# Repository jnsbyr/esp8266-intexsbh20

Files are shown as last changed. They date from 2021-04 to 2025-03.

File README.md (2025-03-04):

# MQTT WiFi remote control for Intex PureSpa whirlpools



### Table of contents

[1. Compatibility](#compatibility)  
[2. Introduction](#introduction)  
[3. Motivation](#motivation)  
[4. Hacking the SB-H20](#hacking-the-sb-h20)  
[5. Building your own WiFi remote control](#building-your-own-wifi-remote-control)  
[6. Contributing](#contributing)  
[7. Licenses and Credits](#licenses-and-credits)

## Compatibility

This projects was originally designed for the Intex PureSpa SB-H20 but it also
supports other models:

 Model                    | Define [^1]  | Notes
 ------------------------ |:------------ |:---------------------------------------------------
 Intex PureSpa SB-H20     | MODEL_SB_H20 | supported
 Intex SimpleSpa SB–B20   | MODEL_SB_H20 | reported to be compatible, see [issue #5](../../issues/5)
 Intex PureSpa SSP-H-20-1 | MODEL_SB_H20 | supported, see [issue #53](../../issues/53)
 Intex PureSpa SJB-HS     | MODEL_SJB_HS | supported, see [issue #13](../../issues/13)

[^1]: #define required for build (see [common.h](src/esp8266-intexsbh20/common.h))

## Introduction

The Intex PureSpa models listed under [Compatibility](#compatibility) are
standalone systems that do not have a remote control option. This projects
provides information about the required hardware and software to provide
WiFi remote control using the [MQTT](https://mqtt.org/) protocol.

This is no ready-to-use product. The acquisition of the required hardware
components, their assembly and programming requires some experience with DIY
 electronics. Helpful details can also be found in the
[issues](../../issues) of this project
(e.g. a table of the hardware components not shown in the schematic can be
found in [issue #2](../../issues/2)).

> :warning: **WARNING**: If you decide to implement the presented solution
  you will void the warranty of your pool as it requires invasive
  modifications. You may only **USE THIS PROJECT AT YOUR OWN RISK**. The
  information provided is meant to be helpful but may contain errors or may be
  misinterpreted. Neither myself nor any of the contributors to this project
  provide any warranty or will assume any responsibility for any damage you
  cause yourself or others by using this project.

## Motivation

Reading the user manual of the Intex PureSpa SB-H20 was a mistake. Everyone
who has ever read a user manual knows this. They just contain things you don't
want to know.

This model seems to be designed for daily attention. It is no news that the
water of a pool should be run through a filter at least once or twice a day.
Many pools have a timer for this, but not this one.

You could keep the circulation on permanently, but this wastes more than 1 kWh
per day with the filter pump consuming around 60 W.

Somehow it should be possible to add a circulation pump timer. And if this can
be done then the water temperature could also be controlled, thus combining power
saving and comfort. Depending on the temperature profile you choose the energy
saving can be really significant compared to a constant temperature setting
because the heater consumes around 2 kW.

## Hacking the SB-H20

Opening the lid of the control panel and attaching a WiFi MCU in parallel to the
buttons was the first idea that came mind. This was possible with the predecessors
of this model, but not so with the control panel of the SB-H20. After testing around
the edges of the case with my pry tools it became obvious that the lid is probably
glued shut. If you want to open it anyway you might consider drilling holes into
the sides of the case first to get better leverage for prying but I did not want
to go that way.

Opening the pump unit and modifying the mainboard did not seem to be a good
alternative either. But there is a cable between the pump unit and the control
panel that might be tapped. Looking around I found the project
[diyscip](https://github.com/YorffoeG/diyscip) from Geoffroy Hubert that gave me
hope. Geoffroy did a splendid job with his reverse engineering but his project
is about the SSP and SJB whirlpool models.

Using a multimeter, a scope and a logic analyser helped to establish several
facts:

- there seems to be a good enough isolation between the mains and the signal lines
  (no guarantee whatsoever)
- the plug and the pinout of the SB-H20 control panel are identical to the SSP
  and SJB models
- most of the decoding of the signals from the mainboard to the control panel
  is identical or at least similar to the SSP and SJB models
- the original control panel and an additional remote control unit can be attached
  in parallel to the mainboard because the signalling supports a multi-drop
  architecture for listening

As Geoffroy did not document any details regarding the button signalling from
the control panel to the mainboard, I assumed from the fact that Geoffroy used
external hardware in addition to the ESP8266 that the SSP and SJB models
require very special handling. As it later turned out, that was not the case,
the button signalling is identical to the SBH model.

Getting all the details of the button signalling right took a while. With the
SB-H20 data clock of 100 kHz it was like searching for a needle in a haystack.
To get 20 data points per clock cycle you need to run the logic analyser with
2 MS/s and this results in 4 million data points for the 2 seconds it takes to
press and release a button on the control panel. Programming an ESP8266 MCU to
provide a hardware trigger for the logic analyser was the key to narrow down where
the action takes place: the control panel pulls the data line low for about 2 µs
after a specific button scan data word was received from the mainboard and this
signalling must be repeated until the mainboard confirms the button action by
enabling the display beeper.

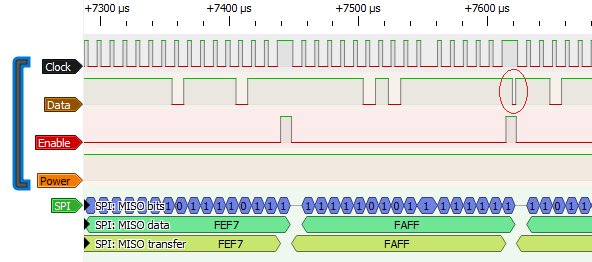
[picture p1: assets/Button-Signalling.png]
Button Signalling SB-H20 button signalling: data is pulled low while enable is high


After testing several variants
the required behaviour could be achieved with a much simpler circuit, that mostly
consists of an ESP8266 and a TTL level shifter for the 3 signals.

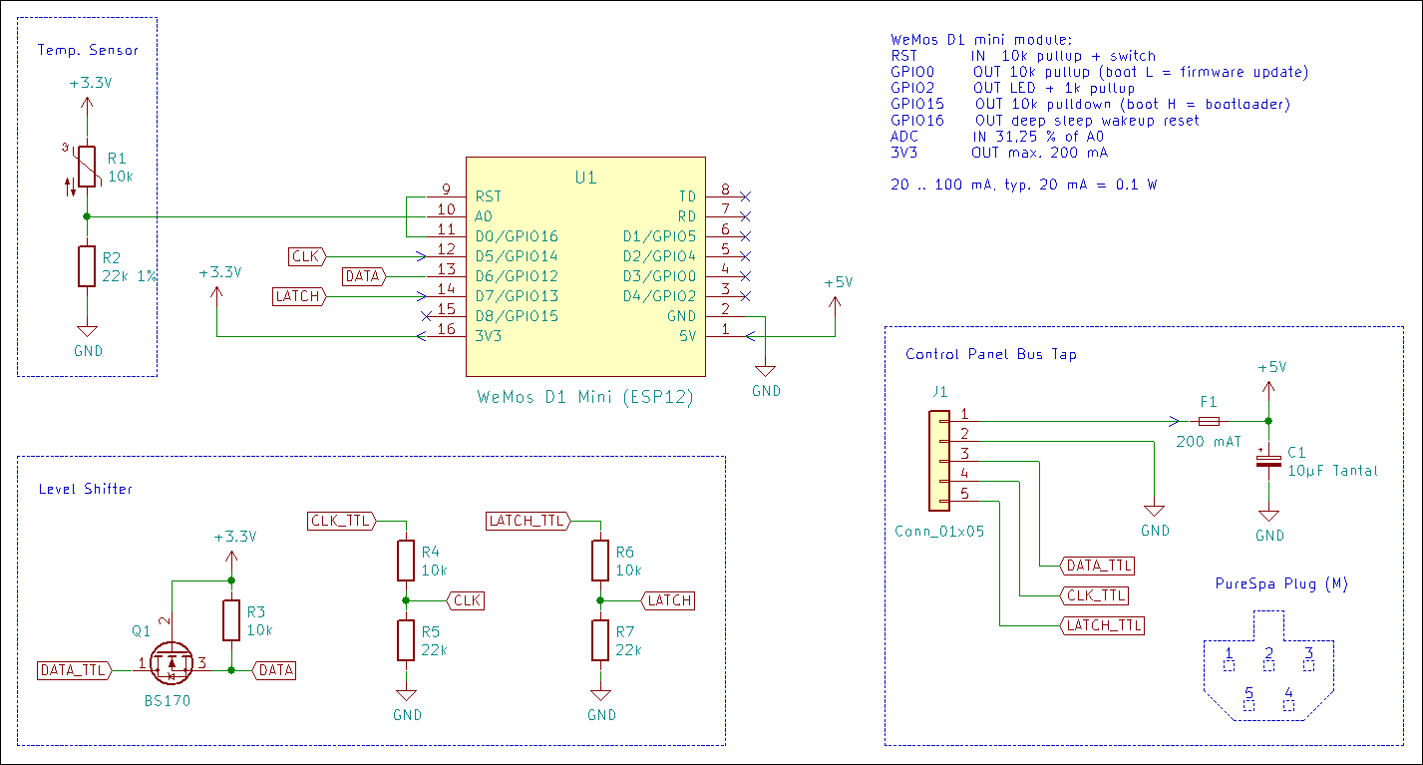
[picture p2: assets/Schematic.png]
Schematic schematic of WiFi remote control for Intex SB-H20


For the button signalling to work, the ESP8266 must be running at 160 MHz to get
the timing right, but that is not all. Geoffroy documented in his code that the
interrupt driven data receive is unreliable but he did not name a reason. The
reason is that the ESP8266 WiFi processing has precedence over all other MCU
tasks and will disrupt time critical processing including ISRs. This is acceptable
for the data receive because the data repeats at a high frequency: incomplete
frames can be ignored and invalid frame data can be filtered out by using only
repeated identical data. But during the button signalling a receive error causes
side effects: a single button press might be ignored or may cause a double change,
and with multiple consecutive button presses the error probability increases
significantly. Activating the ESP8266 WiFi modem sleep while changing the water
temperature improves the receive quality but then the ESP8266 looses its
connection to the AP and the MQTT server for a few seconds with every change.
That is why the latest firmware uses an iterative approach reading back the
new effective setting after each button press and even changing the direction
if an unintentional double change has resulted in overstepping the desired value.

## Building your own WiFi remote control

For the [hack](#hacking-the-sb-h20) described above no modification of the
SB-H20 was needed.

This was good enough for a lab test but not for a permanent solution. To keep the
required modifications of the pool to a minimum there are 2 options to attach the
WiFi remote control to the Intex control panel:

- use an extension cable (needs 2 Intex connectors)
- cut and tap into the control panel cable

### PCB

Depending on your preferences you have several options available regarding the PCB:

- use a perfboard (the ciruit is rather simple)
- use the [PCB design](pcb) from @Elektroarzt
- create you own customized PCB

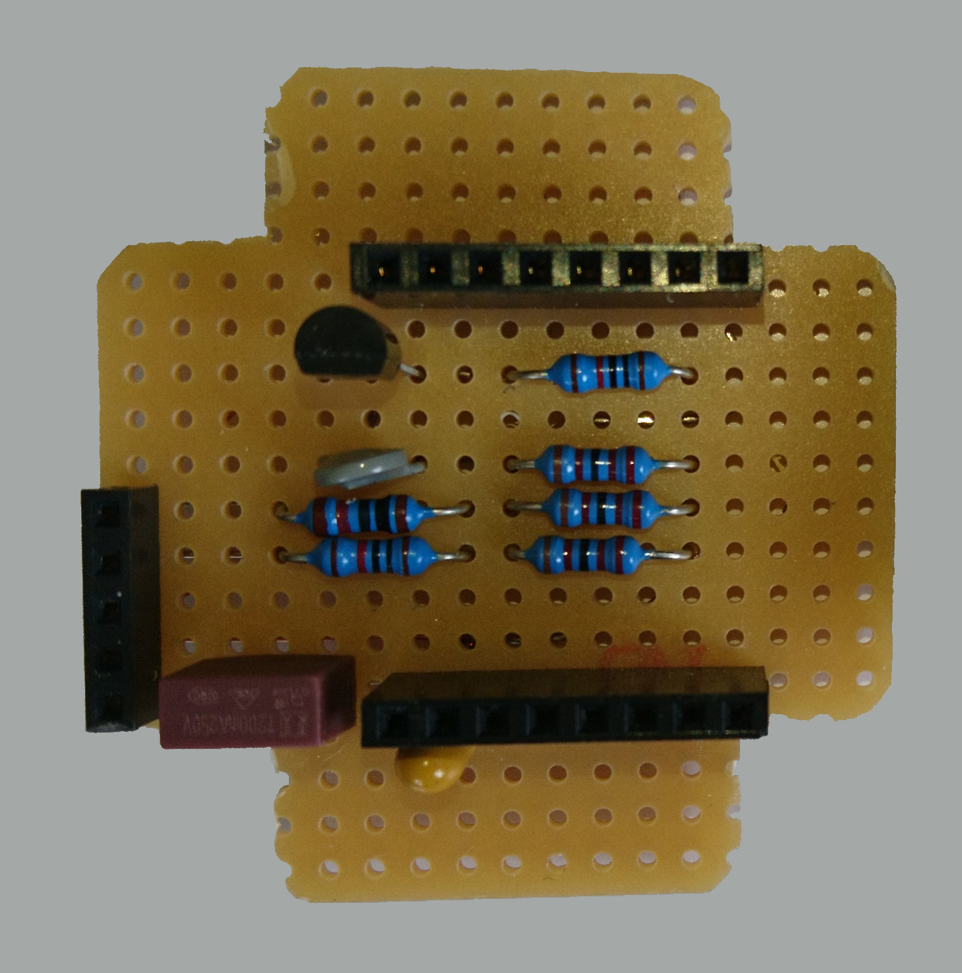
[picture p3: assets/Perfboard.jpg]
Perfboard compact perfboard with sandwich connectors


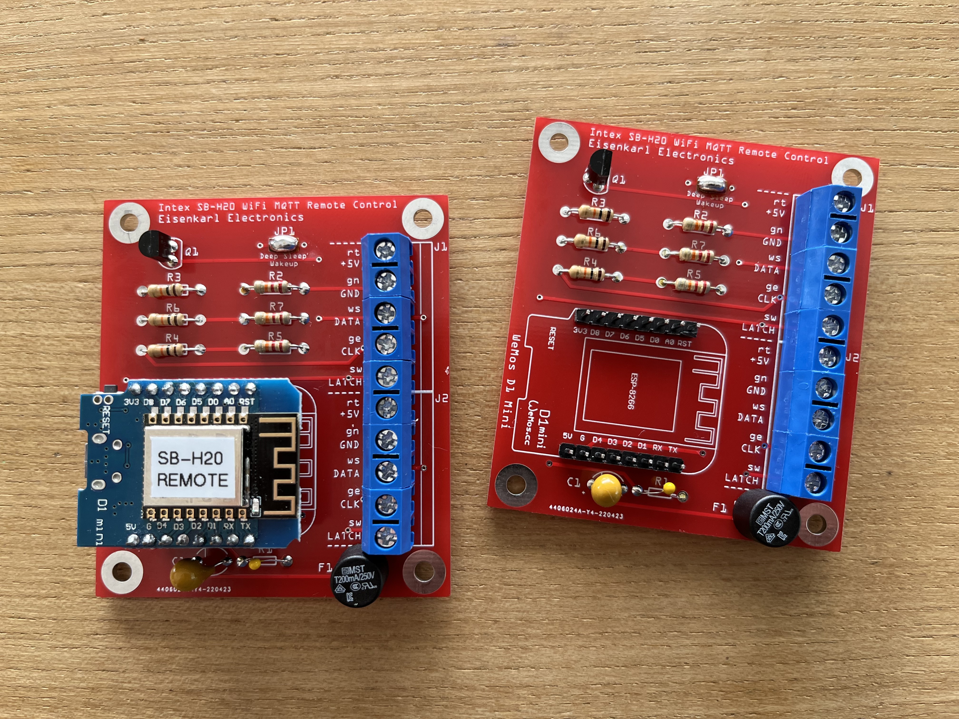
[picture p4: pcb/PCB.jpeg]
PCB PCB with screw terminal


It is not even essential to use the D1 mini, it just makes uploading the firmware
and the config file easier because you don't need an extra USB adapter and a 5 V DC
converter is also included. Any other ESP8266 board with enough ports on the
breakout will do (e.g. ESP12, HUZZAH) but may require slight adjustments to the
circuit and the code.

Before you make a final decision about the board type read the chapter about
the [thermometer](#wifi-controller-thermometer) below.

### Case, Cables and Connectors

Select a case that is IP64 or better to protect the circuit from moisture
and to protect the pool users from electrical shock. The same applies to the
cables and connectors. These components were the most expensive part of the
project at around 30 EUR.

As I could not find a supplier that sells the Intex connectors separately I opted
for the cut & tap option mentioned above:

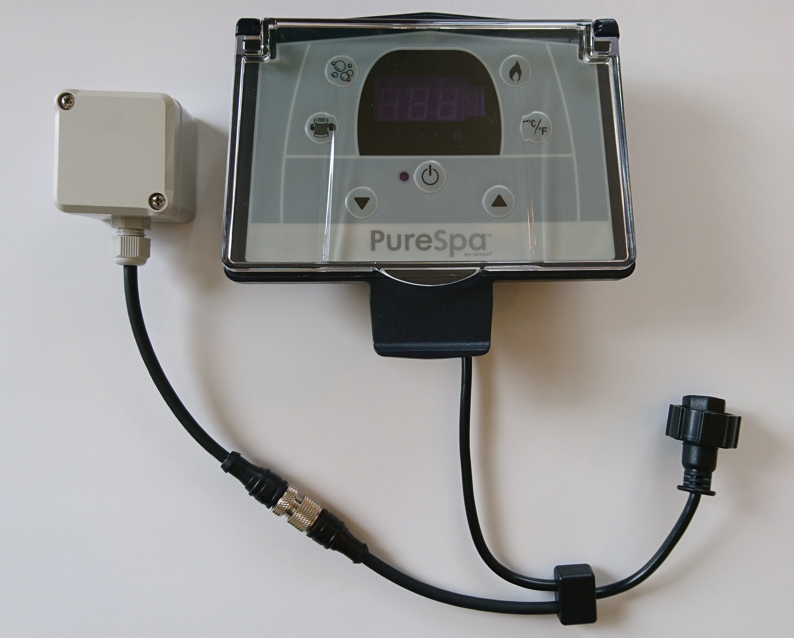
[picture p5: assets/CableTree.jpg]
CableTree modified cable tree of Intex SB-H20 control panel


If you have access to a 3D printer you can avoid cutting the control panel cable.
Have a look at theses models:

- [case incl. Intex PureSpa connectors and mechanical attachment](https://www.printables.com/en/model/509289-intex-purespa-whirlpool-controller-electromechanic)
  for the [PCB](pcb) incl. a detailed assembly info with many photos

- [Intex PureSpa connectors](https://www.thingiverse.com/thing:4130911)

### Power Supply

This project will tap the 5 V DC power supplied by the PureSpa mainboard to the
control panel. Using this power source avoids electrical hazards that may be
introduced by adding an additional mains power supply. A battery might be an
alternative, but with a typical power draw of 20 mA you need a rather large
power pack for a month of continuous operation.

The 20 mA apply if the ESP8266 is able to enter auto modem sleep mode and for
this the communication from and to the ESP8266 must be idle most of the time.
The periodic MQTT publish will interrupt this idle state only for a very short
time with a consumption at 70 mA. The power on current of the circuit is almost
100 mA and if you have a lot of WiFi traffic addressing the ESP8266, e.g.
broadcasts, the consumption might stay at 70 mA.

Beware that the power reserve of the PureSpa mainboard is unknown and that's why
I added a fuse. It is still possible that the extra load of the WiFi controller
may overtax or damage the mainboard. With a consumption of 20 mA the probability
is rather low because a single segment of a 7-segment display alone will consume
a few mA and not all segments are on all the time but the power supply of the
PureSpa should have the reserve for this case.

### Firmware

Select your Intex PureSpa model based on the table in the 
[compatibility list](#compatibility) and comment in the corresponding *#define MODEL_XXX_YYY*
at the beginning of the file [common.h](src/esp8266-intexsbh20/common.h).

If changing the water temperature does not work reliably for you, rebuild the
firmware after commenting in *#define FORCE_WIFI_SLEEP* to use an alternative
method where the WiFi will be disabled while changing the temperature. Note that
this will also interrupt the TCP/IP connection to the MQTT server.

The following **components** are required to build the firmware:

 Component    | Version | Notes
 ------------ |:------- |:-------------------------------------------------------------------------------------------------------
 Arduino IDE  | 1.8     | firmware does not build successfully with Arduino IDE 2.X, see [issue #30](../../issues/30)
 ESP8266 SDK  | 3.1.2   | install using the Arduino board manager
 ArduinoJSON  | 6.21.3  | install using the Arduino library manager
 PubSubClient | 2.8     | install using the Arduino library manager (ignore compiler warnings)

Other versions may also work but are not tested.

The required **board settings** are documented at the top of the INO file. Make
sure to configure them in the Arduino IDE before building.

Note that the firmware uses DHCP and the MQTT server is addressed by hostname.
If you prefer static IPs you must modify the firmware appropriately.

As an alternative to the Arduino IDE you can use Microsoft Visual Studio Code
with one of the following extensions to build the firmware:

- [Visual Studio Code extension for Arduino](https://github.com/microsoft/vscode-arduino)
  and the [Arduino CLI](https://github.com/arduino/arduino-cli)
- [PlatformIO IDE](https://platformio.org/)

### Configuration

Edit the example configuration file *config.json* in the subdirectory *data*.

If you install the [Arduino ESP8266 LittleFS Filesystem Uploader](https://github.com/earlephilhower/arduino-esp8266littlefs-plugin)
you can use the Arduino IDE *Tools* menu to upload the content of the *data*
subdirectory to the MCU. 

When using PlatformIO you should copy the *data* subdirectory from the *src*
folder into the project root folder to be able to use the task "Upload Filesystem Image".

Example:

```json
{
 "wifiSSID":       "WiFi-SSID",
 "wifiPassphrase": "WiFi-secret",
 "mqttServer":     "mqtt.at.home",
 "mqttPort":       "1883",
 "mqttUser":       "userName",
 "mqttPassword":   "password",
 "mqttRetain":     "no",
 "firmwareURL":    "http://webserver.at.home/firmware/SB-H20-WiFiController.bin",
 "errorLanguage":  "EN"
}
```

The config entry *mqttPort* can be omitted and defaults to 1883.

If *mqttUser* is omitted no authentication is used for the MQTT connection and
*mqttPassword* can also be omitted.

If *mqttRetain* is omitted the MQTT messages will be published without the
retained flag set. If defined all values except "no" will activate retaining.

If *firmwareURL* is omitted OTA updates are disabled.

For *errorLanguage* you can choose between "EN" and "DE". If *errorLanguage* is
omitted, the control panel error code will be used.

All other config values are mandatory. If you get a parsing error in the serial
monitor when starting the MCU look closely into your config file. Maybe you
missed a quote or a comma somewhere.

### MQTT

Prepare your MQTT server for a new device.

**Published Topics**

 Topic              | Values                 | Unit | Notes
 ------------------ |:----------------------:|:----:| -----------------------------------
 pool/bubble        | on\|off                |      |
 pool/disinfection  | 0\|3\|5\|8             | h    | SJB-HS only, 0 h = off
 pool/filter        | on\|off                |      |
 pool/heater        | on\|standby\|off       |      |
 pool/jet           | on\|off                |      | SJB-HS only
 pool/power         | on\|off                |      |
 pool/water/tempAct | int                    | °C   |
 pool/water/tempSet | int                    | °C   | -99 °C at power up until set
 pool/error         | string                 |      | error message (see manual) or empty
 pool/model         | string                 |      | metadata
 wifi/rssi          | int                    | dBm  |
 wifi/state         | online\|offline\|error |      | last will topic, offline is retained value
 wifi/temp          | int                    | °C   | inside temp of WiFi module case
 wifi/version       | string                 |      | metadata
 wifi/update        | string                 |      | status message

The topics will be published once after the connection to the MQTT server is established and
then only on change except for the topic *wifi/state*, with a change rate limit of 1 per
second.

**Subscribed Topics**

| Topic | Values | Unit | Notes
| --- |:---:|:----:| ---
| pool/command/bubble | on\|off | |
| pool/command/disinfection  | 0\|3\|5\|8 | h | SJB-HS only, 0 h = off
| pool/command/filter | on\|off | |
| pool/command/heater | on\|off | |
| pool/command/jet | on\|off | | SJB-HS only
| pool/command/power | on\|off | |
| pool/command/water/tempSet | 20...40 | °C |
| wifi/command/update | on | | start OTA update

The *pool* topics are equivalent to the buttons on the control panel of the PureSpa.
Refer to the user manual for more details.

Wait for the next update of the equivalent published topic after each command and
use a timeout to detect command failure. The PureSpa control panel can only handle
one command at a time. The duration for changing the water temperature depends on
the temperature delta.

If *wifi/state* is *error* you are only allowed to send the command
*pool/command/power=off*. The PureSpa will continue to beep for a while. To
clear the error it is necessary to power down the PureSpa.

### WiFi Controller Thermometer

The circuit comes with a NTC sensor for measuring the temperature inside the
waterproof case. The ESP8266 is said to be rather robust (-40 °C to 125 °C)
but this way you are able to monitor the case temperature.

It cannot be avoided that the temperature inside a sealed case will be much
higher than the ambient temperature. For proper heat dissipation the metal
case of the ESP8266 could be attached to a heat spreader. But your options are
limited because you need a plastic case for good WiFi reception and electrical
isolation.

The default settings in the code provide an accuracy of approximately 1 °C
at room temperature and this should be good enough for most use cases.

If you need a higher accuracy you can calibrate the thermometer by providing the
following 4 values that should be measured with a mulitmeter with at least 3 digits
accuracy:

*ESP module not attached to circuit and not powered on:*
- Re: resistance between ESP module A0 and GND
- Rt: resistance between ESP8266 A0 and GND
- Rr: resistance between NTC and GND

*circuit powered on:*
- Vr: supply voltage at NTC

Insert these values into the thermometer setup command in the INO file:

```C++
 thermometer.setup(Rr, Vr, Rt/Re);
```

Some ESP modules do not come with a voltage divider for A0 (Re and Rt > 1 MOhm).
In this case you need to add your own voltage divider because the ESP8266 analog
input is limited to 1 V.

### Power On

Connect the WiFi controller to the PureSpa. Verify the pinout before
powering up the pool. After power up the control panel should operate
normally. The WiFi controller should connect to the AP, receive an IP address
and connect to the MQTT server within a few seconds. If this was successful it
will report the current status of the pool to the MQTT server.

### Troubleshooting

In case of an error you should check the logs of your AP and your MQTT server.
If the WiFi controller connects to the MQTT server successfully but reports
offline state you should check the pinout again, preferably with a scope.
If this does not help you should use the serial monitor of the Arduino IDE
and you can activate additional serial debugging in the firmware.

### Operation and Security

Security aspects are typically not the focus of a DIY project and the basics
for the electrical security have been mentioned above.

Regarding the network security of the project you will notice that it does
not include a webserver. At first glance this seems to reduce the usability.
But you need the Aruduino IDE anyway to build and upload the firmware and
uploading the config file with the Arduino IDE as a second step is seamless.
And if you still want a webserver, it should not be that hard to add.

Not enabling the webserver is a security improvement because it is nearly
impossible to harden the webserver on an IoT device. That is why the project
only uses TCP/IP clients with predefined servers: One is the MQTT client and
the other is the OTA client. In this configuration a hacker must take over
significant parts of your network and if he got so far then he cannot be stopped
anyway if he knows what he is doing.

So just make sure that your MQTT server UI is secured properly and you will not
find your pool cover blown off because a guest turned on the bubbles while the
cover was closed.

One up would be to use encryption for the MQTT communication but the MQTT
client library currently does not support it.

## Contributing

If you want to contribute to this project, please have look at the 
[contributing guide](CONTRIBUTING.md) first. It will provide guidelines for 
creating [issues](issues) and [merge requests](pulls).

## Licenses and Credits

Copyright (c) 2021 [Jens B.](https://github.com/jnsbyr/esp8266-intexsbh20)



The code was edited with [NetBeans](https://netbeans.apache.org/).

The firmware was build using the [Arduino IDE](https://www.arduino.cc/en/software/).

The schematic was created using [KiCad](https://kicad.org/).

The signal analysis was aided by [PulseView](https://sigrok.org/).

The badges in this document are provided by [img.shields.io](https://img.shields.io/).

The firmware source code depends on the following projects:

#### ESP8266 Core

Copyright (C) 2015 [Arduino Core for ESP8266 Project](https://github.com/esp8266/Arduino)



Parts of the "Arduino Core for ESP8266" project have different licenses, see the project description for more details.

#### ArduinoJson ####

Copyright (C) 2014 [Benoît Blanchon](https://arduinojson.org)



#### LittleFS ####

Copyright (C) 2017 [Arm Limited](https://github.com/littlefs-project/littlefs)



#### PubSubClient ####

Copyright (C) 2008 [Nicholas O'Leary](https://github.com/knolleary/pubsubclient)



The concept of this project and parts of the firmware are based on:

#### DIYSCIP

Copyright (C) 2020 [Geoffroy Hubert](https://github.com/yorffoeg/diyscip)



#### PCB

Copyright (C) 2022 [Elektroarzt](https://github.com/Elektroarzt)



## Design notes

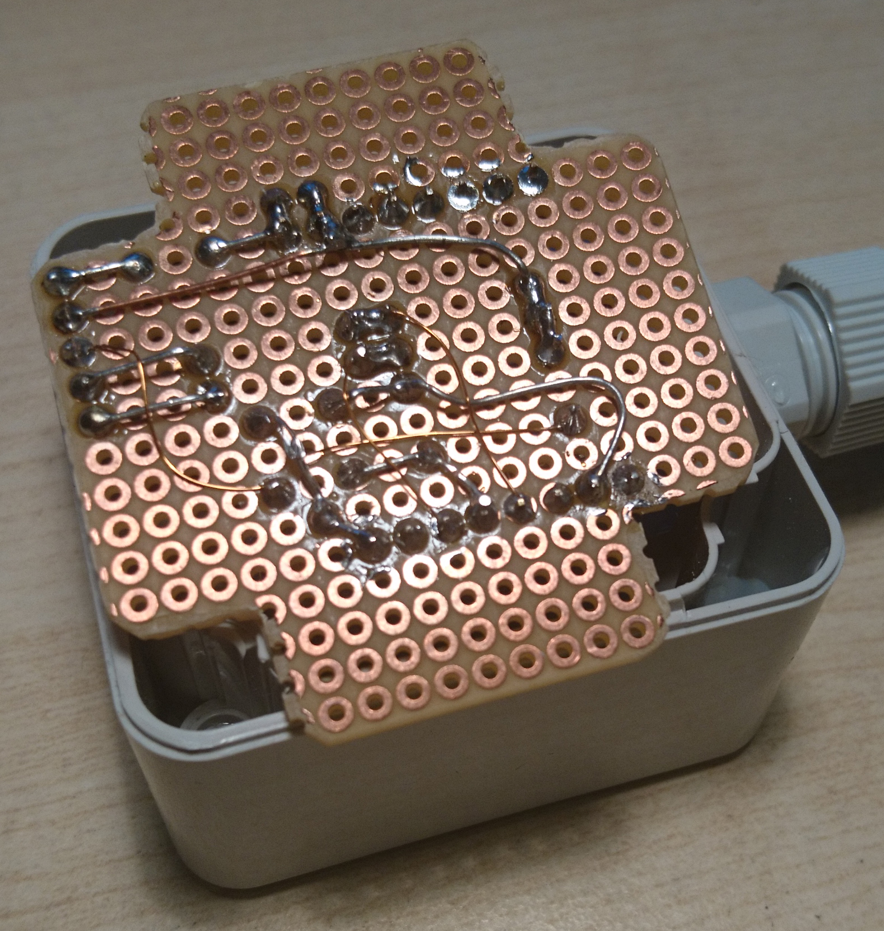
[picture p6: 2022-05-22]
assets/Perfboard Bottom.jpg

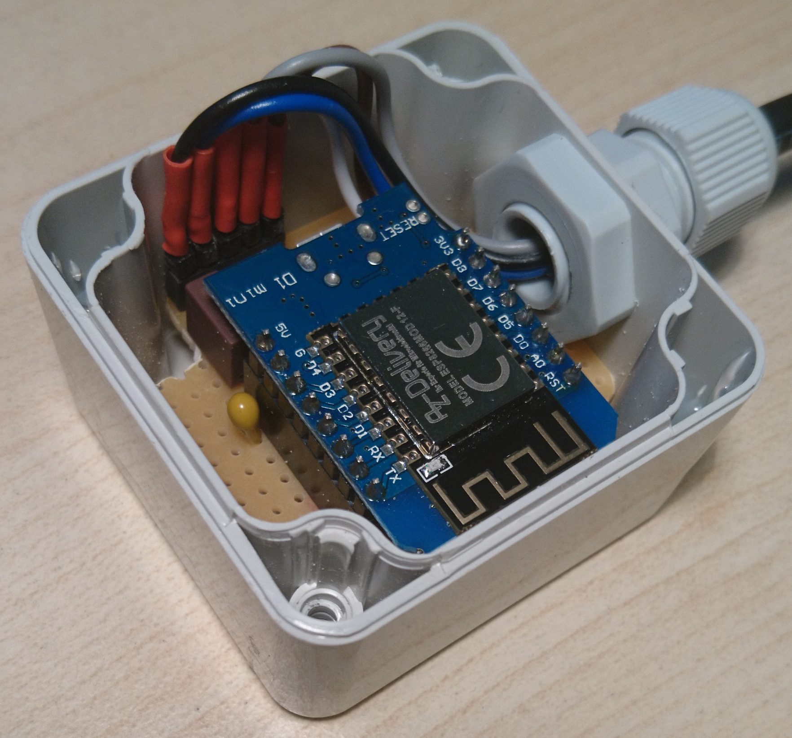
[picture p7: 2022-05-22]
assets/Open Case.jpg

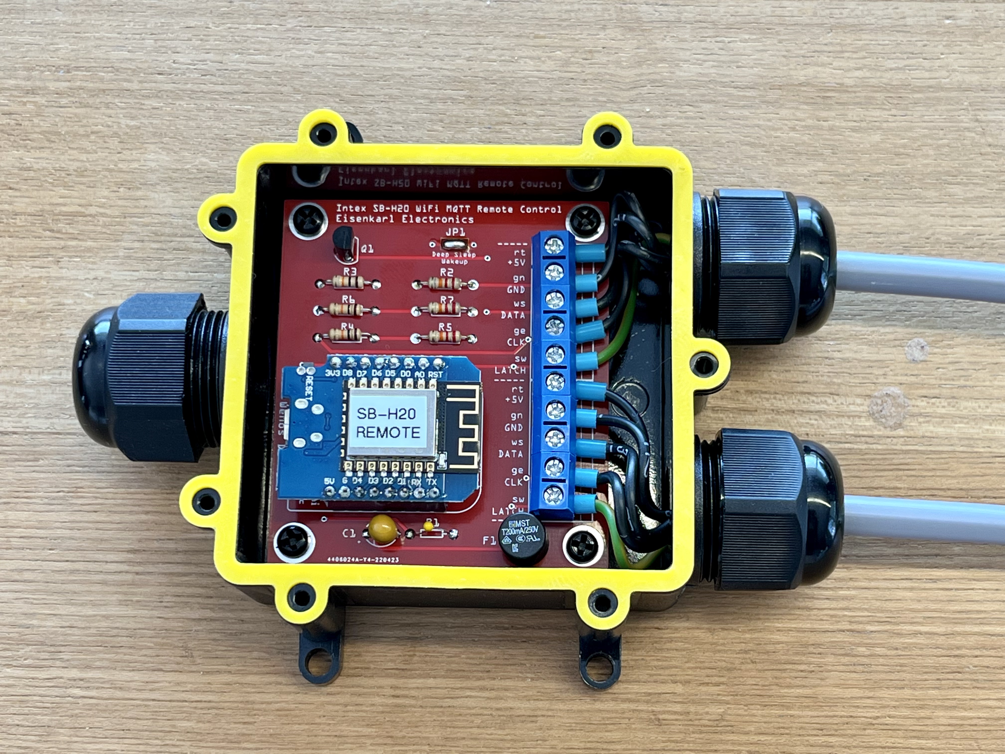
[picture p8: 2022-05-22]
pcb/PCB-With-Housing.jpeg

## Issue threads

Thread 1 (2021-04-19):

How to build without electronic background?

stevoh8494, 2021-04-19:
Hello, It's a really good work man, so again congratulations. I've the same spa and I'm really interested in connecting it to my home system.
But electronic is not my speciality. :(

- How can I build it easily?
- do you have references of each component used?
- Do you have more pictures that can help me?

Sorry, too much questions :)

jnsbyr, 2021-04-20:
I am sorry, but if electronic is not your speciality I suggest you should not start with this project. And electronic skills will not be enough, you also need electromechanical skills for the watertight case and cables. Take the warning in the readme seriously. You have to create a reliable solution for the combination of water and electrical power. A pool should be a place for fun, so make sure to keep it that way. But it is not only about electrical security. You should also know how to handle a multimeter and soldering iron, otherwise frustration is guaranteed.

If you feel you are up to the task you can simply use the component values from the schematic. All necessary info is included. Any good electronics retail will be able to supply them. In the photo of the perfboard you can even see how the components look like. There are no other photos. I never intended for anyone to rebuild it exactly in the same way. The idea was to show that it can be done. So you are free to use completely different components especially for the case and cables. If you need some more info, have a look at the solution for the other Intex models from [Geoffroy](https://github.com/yorffoeg/diyscip). Note that even with the necessary experience you will need around 2 working days for assembly and testing.

If you still want to continue, get yourself the required electronic components and a breadboard and make it work on your desk. This will probably take a while and it will get really messy when you try to connect the breadboard with the spa connector. Try to do it in the beginning without cutting into the cables of the spa, unlike I showed in the photo, but use a temporary solution. When I started with the hack, I placed very thin insulated wires with uninsulated ends into the female part of the plug of the control panel and fixed them in place by attaching the control panel again. With this kind of tap you can test your circuit and see what happens without mechanical damaging the spa. But this improvised tap has the disadvantage that you might easily short circuit the signal and power lines. I never tried to find out what happens. Maybe you will need a new spa mainboard.

I don't know anything about your capabilities so please don't take my explanation the wrong way. I hope it helps to put the project into the right perspective.

Closed 2021-04-24.

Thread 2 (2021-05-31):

Need more information

PaTiTan, 2021-05-31:
Hello,
You are doing a great job.

Can you give us the list of components?
Also general diagram of all the architecture because I do not know if your module is in parallel or in series.
Thanks

B4n4n3, 2021-05-31:
Hello jnsbyr,

thanks for your great job!
Can you post the links to the german stores for the components?
i am interessted in

- IP64 case
- connector and cables

thanks a lot!

jnsbyr, 2021-05-31:
Here is a list of the components that are not obvious from the schematic:

| description | part no. | URL |
| - | - | - |
| main case | BOPLA ET-205 | https://www.reichelt.de/de/en/housing-52x50x37-mm-bopla-et-205-p5725.html
| y splitter case | RX2003-S-5 | https://www.reichelt.de/de/en/kunststoffgehaeuse-26-x-18-x-13-mm-5-stueck-rx2003-s-5-p292742.html
| 5pin M12 plug with cable | LUT 1210 05 06 | https://www.reichelt.de/de/en/sensor-cable-m12-5-pin-male-female-0-6-m-lut-1210-05-06-p223002.html
| PG cable gland | PGBF 7 | https://www.reichelt.de/de/en/cable-gland-pg-7-3-6-5-mm-pgbf-7-p126186.html
| PG lock nut | PGGM 7 | https://www.reichelt.de/de/en/locknut-for-pgbf7-pggm-7-p126192.html?search=PGGM+7&&r=1
| 10k NTC | EPC B57164-K103 | https://www.reichelt.de/de/en/ntc-resistor-450-mw-10-kohm-epc-b57164-k103-p240041.html
| fuse | ESKA 883.110 | https://www.reichelt.de/de/en/radial-fuse-time-lag-t-200ma-square-eska-883-110-p279212.html

jnsbyr, 2021-05-31:
@PaTiTan
> Also general diagram of all the architecture because I do not know if your module is in parallel or in series.

Please have a look at the schematic. It shows a block named "Control Panel Bus Tap". It should imply that the circuit is connected in parallel. In the description above this is mentioned explicitly "the original control panel and an additional remote control unit can be attached in parallel to the mainboard because the signalling supports a multi-drop architecture for listening".

You may also have look at the top left of the [schematic from Geoffrey](https://github.com/YorffoeG/diyscip/blob/master/docs/schematic_PCB_V2.jpg).

Hope this helps.

jnsbyr, 2021-05-31:
Application note for the assembly of the y splitter case:

The part mentioned in the table above is tiny in comparison to the dimensions of the cable. The drill holes I used are a little smaller than the cable diameter to make them self sealing. Originally I planned to fill the case with epoxy to prevent the cables from being pulled out accidentality and to make it waterproof. But the fit was so tight that it was not really necessary. The cable ends need to be soldered together. To prevent a short circuit the open ends must be isolated again, e.g. using shrink tubing.

If you don't intend to spend more than an hour on this item, use a case with a volume at least 3 time larger instead. You might even skip the soldering if you use a ready to use connector with screws or clips.

B4n4n3, 2021-06-01:
Thanks a lot for the partlist. Did you use the original cable (mainboard <-> controle panel)?

jnsbyr, 2021-06-01:
Yes, please have look at the photo of the 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. Looking from the position of the y spitter case:
- the "center" cable to the control panel is about 2/3 of the original cable from the mainboard to the control panel
- the "right" cable with the Intex plug is about 1/3 of the original cable from the mainboard to the control panel
- the "left" cable to the WiFi controller is the M12 cable from the component list, approximately split in half

PaTiTan, 2021-06-05:
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
but what is this grey thing?

jnsbyr, 2021-06-06:
You might have guessed by elimination that this must be the NTC. You can
also use the link in the component table for another image of the same
component. NTCs come in various makes and sizes. I chose this because it
was cheap and comparatively robust (large). Any other 10k NTC will do.

Am Sa., 5. Juni 2021 um 18:30 Uhr schrieb PaTiTan ***@***.***
>:

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

PaTiTan, 2021-06-08:
last question : where is number 1 pin ?
Left or right connector :
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

PaTiTan, 2021-06-08:
The "command" dont appear so do it myself but i dont understant how work this command :

`pool/command/water/tempSet | int | °C`

i just want to increase or decrease or put a value of température wanted
I need something too is what température i have ordered. (pool/water/tempAct is what temperature is inside).

thanks for your incedible job !!

jnsbyr, 2021-06-08:
> The "command" dont appear ...
This is an aspect of your MQTT server. Typically you need to define the MQTT topics that are to be send from the server to the client on the server side and these kind of topics typically contain the label "command". So here you need to enter all entries listed under "Subscribed Topics" in the readme.

Once you have established a connection between the spa WiFi controller and your MQTT server you should be able to set any of the "Subscirbed Topics" on the server side. You can use serial debugging to check if the ESP8266 is receiving the MQTT command data.

> I need something too is to see what température i have ordered. ...
With the topic "pool/water/tempAct" you have made the right choice. The spa WiFi controller will send it after the connection is established to the MQTT server and to the spa mainboard.

jnsbyr, 2021-06-08:
> @PaTiTan Where is number 1 pin? https://user-images.githubusercontent.com/69749534/121177003-2dbff280-c85d-11eb-8466-3abf5e1a9a3a.png

In the schematic there is an abstract drawing of the plug titled "PureSpa Plug (M)" in the bottom right corner. The "M" stands for "male" and such a plug should have pins. The schematic shows the plug from its front side. So, looking at your images of the two plugs, the left one would be the M-type (with the contact pins missing) while the right one would be F-type. The socket in the Intex pump housing is the F-Type while the Intex control panel cable has a plug with the M-Type.

PaTiTan, 2021-06-09:
maybe use this from diyscip ;)
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

anyway, THANK YOU SO MUCH for you awesome great work !
is working well (exept for ordering temperature with Jeedom via jMQTT).

jnsbyr, 2021-06-09:
> @PaTiTan ... exept for ordering temperature with Jeedom via jMQTT

Thank you for your feedback, I am glad that you like this project.

The drawing of the plug from Geoffroy is good, but I didn't want to copy it
and I am not much of an artist myself.

You say that setting the temperature is not working for you. That's sad
because that was one of the major reasons I started this project. I cannot
help you with anything that is Jeedom specific, but if you are interested
in making this work I will try to help. First you must establish if the
MQTT command for the setpoint temperature reaches the WiFi controller.
Connect TX+GND of the ESP8266 to an TTL/USB converter connected to your PC
and open a serial terminal (e.g. PuTTY) with the serial parameters
74880/8/N/1. Every time you send an MQTT command from Jeedom you should see
a serial output looking like "set: <topic>: <value>". If not, the problem
is probably on the Jeedom side. If the topic "pool/command/water/tempSet"
is received and the value looks OK then contact me again.The value must be
an integer number, it should not contain a decimal point.

PaTiTan, 2021-06-10:
Tanks a lot, it was Jeedom MQTT :)
All work really good.

Thank you so muck, you are the best!!!

JonOLinux, 2021-06-15:
Hello jnsbyr
Thank you for your great work and for sharing.
I have a SBH-20 and I would like to domotize it, do you sell the card please ?
thank you

jnsbyr, 2021-06-15:
@JonOLinux
Sorry, I cannot help you in this respect. Please read the Readme.md again. This project was started primarily as a proof of concept. I have not designed a PCB but used a breadboard for the prototype. It is working for me and there is no necessity for me to replace the breadboard with a PCB.

You could use a tool like KiCad and design your own PCB - but really, you don't need it. The circuit has only a few component and you need to solder anyway, so adding a few wires on the backside of the perfboard should be no big deal. It only takes a little longer than using a breadboard.

JonOLinux, 2021-06-15:
Ok, I will do it.
Thank you for your help.

________________________________
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

jnsbyr, 2021-06-16:
@JonOLinux
If you decide to design a PCB for this project, please consider adding it to this repository (e.g. as a merge request). It will certainly make someone else happy.

stevengoossensB, 2021-07-06:
Hi @jnsbyr

Could you share a picture of the backside of the perfboard and how it's soldered together as a reference? I'm trying to understand how to connect all components in the picture (https://raw.githubusercontent.com/jnsbyr/esp8266-intexsbh20/master/assets/Perfboard.jpg) in a clean manner without unwanted interconnections.

jnsbyr, 2021-07-07:
Hope the picture I was able to make will help. The left is still left but the bottom of the top side picture is the top of the bottom side picture. A 3D picture of the perfboard wiring would be better suited, but alas, that's not done with a click.

There are a total of 4 isolated thread wires for crossovers, all other connections are without crossovers or use pad to pad soldering. I tried to make use of all the wires that come with new components. I a few cases it was enough to just bend them first and cut them off at the next component pad.

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

And here is a picture of the open case that shows how the M12 cable connects to the board:

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

stevengoossensB, 2021-07-09:
Many thanks, this is really helpful!

Matze5593, 2023-05-11:
Hello,

could someone tell me more about the tendal capacitor?

Tantalum capacitor, 10 µF, 16 V, RM 2.5

What voltage should the capacitor have?

https://www.reichelt.de/tantal-kondensator-10-f-16-v-rm-2-5-tantal-10-16-p20332.html

jnsbyr, 2023-05-11:
> What voltage should the capacitor have?

Looking at the schematic, the cap is connected to +5V nominal, might be around +5.25V for real.
Looking at the datasheet of the linked cap the +10V version is rated for a surge voltage up to +8V. This would be the minimum recommeded value. Any higher value will also work.

Closed 2021-07-26.

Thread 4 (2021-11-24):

Need some code explanation

titolini72, 2021-11-24:
Hi Jens,
I drop you a request after someone told me about your work. Really nice actually !!
I already start the same project but from Jof. I follow the schematics from his GitHub but today it doesn't work
- MQTT is ok (verified) : Rx and Tx
- Decoding frames are ok as well
- Nonetheless button press simulation are not ok at all; and honestly I don't understand the schematics base on SN74HC595 and CD4051.
-
You solution has the main advantage to perform everything from ESP8266 in sw.

However reading your code I don't understand how it works though :) The main question is how you emulate the "Press Button"
Starting from `poolIO.setPowerOn` (MTTQ Cmd) for example
`pressButton(buttons.togglePower); `(Still ok)

How this simple statement ends up to a "Power on button press" ?!?
I see `ICACHE_RAM_ATTR inline void SBH20IO::decodeButton()` but here I don't get how this works either
If Power On is for instance Off, I assume `else if (isrState.frameValue & FRAME_BUTTON::POWER)` is false. ... so my interrogation

Would you mind to clarify this point please

Thanks in advance and best regards

jnsbyr, 2021-11-25:
Hi titolini72,

I will try to help you. I didn't get how Jof's hardware works, either, and he didn't answer my questions.

The whole process of signalling a button action is really time critical. The only way to handle this asynchronously with a MCU is using an ISR.

So the method `pressButton()` itself does not do much except setting the control value `buttonPressCount` and monitors if the control value changes. `buttonPressCount` is the parameter of `pressButton()` but is not a value parameter but a reference parameter. This results in modifying the values of the `Buttons` struct. Look into the ISR method `SBH20IO::decodeButton()`. Here the `Buttons` are handled by changing `isrState.reply`. And at the end of the method `PIN::DATA` is pulsed.

Hope this helps.

titolini72, 2021-11-26:
> he didn't answer my questions.
Well I had told with him by phone w ... after the call he never replied to any inquiries : SMS, Phone ,e-mail ... doh
> The only way to handle this asynchronously with a MCU is using an ISR.
of course

Given you explanation, this is my understanding of the code ... so my misunderstanding on how the code should behave.
Let me give you an example
Let say I want to Power on the SPA via MQTT command (`setPowerOn` function) . This commend is supposed to set bit 0x0400(bit 10) in the 16bits frame (Button Power on).
`SBH20IO::decodeButton()` is called at the very end of the frame, I mean after receiving the 16 bits of the frame.
**Where this bit 10 is pulled or toggled ?**
Assuming the SPA is OFF, the flag FRAME_BUTTON::POWER is obviously at 0, the reply is obviously at false ... so my confusion :)
` And at the end of the method PIN::DATA is pulsed.` Again confusion :) Pull Up ? Down ? by setting DATA as output create a Pull Down ? BS170 converts this value in 0V TTL ?

I am very sorry for having so many questions. I hope you are not too upset by such inquiries.
Best regards

jnsbyr, 2021-11-26:
> Let say I want to Power on the SPA via MQTT command (`setPowerOn` function) . This commend is supposed to set bit 0x0400(bit 10) in the 16bits frame (Button Power on).

No, you are looking at this project from the perspective of Jof's project and Jof never claimed that his project is suitable for the SBH20. Check my [screenshot form the digiscope](https://github.com/jnsbyr/esp8266-intexsbh20/blob/master/assets/Button-Signalling.png) and look for the pulse on the data line that is manually marked in red. The pulse comes **after** the data that asks "Is butten XXX pressed?". If the pulse is send after the data (during the clock break) with the right timing, it is accepted as a "yes".

The BS170 works as a bidirectional level shifter. Most of the time the ESP8266 only receives bits (high impedance input). When a pulse must be sent back the data output is temporarily activated and set to low and this also makes the data line go low.

titolini72, 2021-11-27:
`No, you are looking at this project from the perspective of Jof's project `
Yup it looks like. I thought it was the same though.
`The pulse comes after the data that asks "Is butten XXX pressed?".`
I will put my scope as well. it looks like the button are scanned by the server. The pull is just to confirm the scan. Let me see that ;)
`The BS170 works as a bidirectional level shifter. `
Gotcha I have a BSS138 at my end that works for this same purpose. The main difference is this is surface mounted devices.  Nothing else.

As a conclusion, I believe the design from Jof can be used (I mean I can "reuse" the PCB I have by no using a part of it. On ly Sw has to be changed). I will investigate and let you know

BTW thanks for all these valuable inputs

Regards

jnsbyr, 2021-11-27:
Glad I could help and I agree that it should be possible to make use of the PCB from Jof for this project by not using the the CD4051BE and SN74HC595N components, but it might be necessary to interrupt the connection of the DATA/CLK/HOLD-TTL signals to these components to avoid side effects.

titolini72, 2022-01-10:
Hi Jens,
Mixing Jof's code and yours I end up in a working solution. The PCB 3/4cm is on the way to finalize.
If I keep Jof's code, this is because how CFG is managed (Web interface to setup Wifi and EEPROM to store data). However the Control Panel is all yours ! I tried to upgrade Jof's but this was a disaster. Copy/Paste + adaptation was the best option

Thanks for your help we can close the issue ;)

Closed 2022-05-08.

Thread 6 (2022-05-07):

Node Red Flow

Elektroarzt, 2022-05-07:
Hi Jens,
big congrats to you for your excellent work! I got the PCB with a D1 Mini to work and made an integration in HomeKit via Node Red which is beta at the moment. Did you - by chance - also made some Node Red Flows behind your MQTT Broker? If so, I would be very interested in this for my reference.

As I made a PCB out of your schematic (tested design) I also like to share Fritzing and Gerber data if you like to reshare in your repository for free usage in the community. If you are further interested in a ready-to-go PCB, please let me know and I will send you one or two.

Thanks and best regards,
Thomas

jnsbyr, 2022-05-08:
Hi Thomas,
thanks for taking an interest in my little project from last spring.
I did not play around with Node Red so your on your own here. I will keep this case open, maybe someone will see your request.
Regarding your PCB design I would prefer your direct participation, if this is OK for you. I already added you as as collaborator to the project. If you go ahead with this idea, you should let me know how much experience you have with Git. If you are not familiar you should
- install the GitHub app on your computer
- checkout the project
- create a new folder named "pcb" on the main level and put the PCB related documents there
- push your update to a new branch, e.g. name it PCB
- create a merge request
If you already know how it works you can commit directly. After your files are included I would like to add some references to your document to the Readme.

Elektroarzt, 2022-05-08:
I'm not a frequent GitHub user but I think I got it, thanks for your quick start guide. Please have a look if everything fits for you and if you need something from me for the readme or so.

Best, Thomas

fizcris, 2022-06-12:
Hey @Elektroarzt could you add links to get the waterproof box?
Also it would be great to know if you have a PCB lying around so I don't have to manufacture 5pcs to use one.

Elektroarzt, 2022-06-12:
Hi fizcris ... I used the following components for the case:
- Case: Anicoll M686 IP68 (e.g. https://www.amazon.de/gp/product/B075XHW4LS/ref=ppx_yo_dt_b_asin_image_o01_s01?ie=UTF8&th=1)
- Mounting spacer: Standard M3 nylon hex distancer (e.g. https://www.amazon.de/gp/product/B06Y43YY1B/ref=ppx_yo_dt_b_asin_title_o04_s00?ie=UTF8&psc=1), which can be glued in the case easily

As I have a bunch of friends - meanwhile all with the same pool :) - I assembled some pieces as a batch. So unfortunately I don't have a blank PCB but fortunately I have some complete devices left from the batch for self cost (assembled PCB / case / spacer / D1 Mini). If you are interested write a PN under elektroarzt@digital-filestore.de

Regards, Thomas

Elektroarzt, 2022-07-10:
Hi to all pool lovers :)

meanwhile I have a Node Red flow that works like a charm I like to share. It has the following features up to now:
- bridge to Apple HomeKit for remote control via mobile devices (see photo)
- web interface (see photo)
- configurable charts for  pool temperature, ambient temperature, energy cost, heater power
- timer for desired ETA with date and time
- timer for pool chemicals (5in1 chloride tabs)
- timer for automated daily filtering
- failure and status message via telegram

The code is stable but at certain points improvable, e.g. the user interface.
@jnsbyr: if you agree, I would upload the flows

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

jnsbyr, 2022-07-10:
Looks really good, and I think the timer is a useful extra feature.

Please add a separate subdirectory (e.g. nodered) for the files. If there installation requirements, please add an additional readme into the nodered subdirectory too.

We should also add a new paragraph about the Node-RED support to the Readme. My ideas to put some (or all) of the screenshots above into the assets subdirectory (e.g. with file name prefix NodeRed) or into the nodered subdirectory. Then the Readme can get updated to show the screenshots and give a short introduction.

jnsbyr, 2023-08-11:
@Elektroarzt: If you still think adding the Node Red flow to project is a good idea, please proceed or close this issue.

Elektroarzt, 2023-08-14:
Up to now there were no questions concerning Node Red integration and I feel ioBroker and Home Assistant are the most common ways to implement the pool controller on backend side. Node Red seems a little exotic. So you are absolutely right and I close this issue.

Closed 2023-08-14.

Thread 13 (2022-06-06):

Support for Intex SJB-HS

Monsardi, 2022-06-06:
Hello,
I have a intex sjb hs with salt electrolyse + jet streams.
Do you think it is possible to add this functionality?

all the best Peter

jnsbyr, 2022-06-11:
@Monsardi
The display of the SJB-HS looks different than that of the SBH-20, e.g. it has additional buttons. Without getting my hands on the hardware and spending some time with it it is impossible to say for sure.

Please have a look at the project [DIYSCIP](https://github.com/yorffoeg/diyscip) because it claims to support SSP-xxx and SJB-xxx models.

mabeca96, 2022-07-10:
Hello
I also have an Intex SJB.
I connected the esp8266-intexsbh20 project to the pool.
I just have the problem that I can't turn the filter on and off.
When I turn on the filter via ESP, the bubble turns on.
The info what on/off is correct.
Also the temperature is displayed correctly

jnsbyr, 2022-07-10:
@mabeca96: That is very interesting. I did not expect that it would work at all.

On the assumption that the control principle of my project also works with the SJB model, some changes are required to address the different mapping of the control function like the bubbles. The approach would be:

- add a new config option to select the Intex model (SBH, SJB)
- support different control bit mappings for each supported model

Because I do not have a SJB I would prefer is someone changes the code, makes tests and submits a merge request. Otherwise I would have to dry code and you could test. My current lack of spare time will not allow me to do the latter, at least not before the summer is over.

Luckily there is another option: you could hard code the changes yourself. That way we will quickly know if it really works. Open SBH20IO.cpp and change the values in the enum _FRAME_BUTTON_. Look into the project [DIYSCIP](https://github.com/YorffoeG/diyscip/blob/master/src/CTRLPanel.cpp) to get the correct values or just try out different values. You already know that the current value of the filter is your value for the bubbles.

Let me know if you can make it work this way and if yes, post the details of the changes you made.

mabeca96, 2022-07-11:
I will try it with hard code.
Can you help me see the value of DIYSCIP?
Example
You: const uint16 POWER = 0x0400
DIYSCIP: BUTTON_POWER U5 | COMMAND_ADDRESS_S2
BUTTON_POWER COMMAND_ADDRESS_S0
#define U5 0x80
#define COMMAND_ADDRESS_S4 0x04

Monsardi, 2022-07-11:
Thanks for jumping in the conversation. I can confirm that I have the same buttons/functions that work and the same that fail.
Pushing the bubble function triggers the jetstreams and the filter is triggered by the bubble button.
Of course there's also nothing that triggers the salt electrolyse.
I'm curious whether the hard code road will work!

jnsbyr, 2022-07-13:
When I look into the DIYSCP code I don't see a definition for a bubble or a jet button and there seems to be no additional documentation other than the code and the schematic. So I don't have anything to compare or recommend.

Please assign an otherwise unused 4digit hex value that sets only 1 bit (1, 2, 4, 8) to one or more of the functions of FRAME_BUTTON (e.g. 0x0100) which do not work for you, build and try these functions. Should be around 16 possibilities - so this should not take too long. Either it helps or it doesn't. Beware that this way you might be able to send a code that triggers a function reserved by the manufacturer that cannot be triggered by the real panel.

Regarding functions the SBH model does not support like the electrolyse - if you can find the button code and it works consistently for you than let me know.

mabeca96, 2022-07-25:
I found out the following code

  const uint16 POWER     = 0x0400;
  const uint16 FILTER    = 0x0080;
  const uint16 HEATER    = 0x8000;
  const uint16 DESIFECT  = 0x0001;
  const uint16 TEMP_UP   = 0x1000;
  const uint16 TEMP_DOWN = 0x2000;
  const uint16 TEMP_UNIT = 0x2000;
//  const uint16 JetDuesen       = 0x0008;
//  const uint16 JetBubble       = 0x0002;
//  const uint16 F-C     = 0x2000;
//  const uint16 JetBubble       = 0x0002;

what I am still missing is the display whether the disinfection is on or not.
Can someone explain to me where I have to set additional entries to control them from the MQTT (e.g. disinfection)

Monsardi, 2022-08-05:
have you found out the missing entries?
Unfortunately I have no knowledge at all aboit coding so I can't be of any help.

jnsbyr, 2022-09-05:
> I found out the following code
Did you try the setting you posted by changing FRAME_BUTTON in SBH20IO.cpp?

If yes, please elaborate your results a little bit. Your current listing has some contradicting lines e.g. TEMP_DOWN and TEMP_UNIT are both 0x2000. Can it be that you do not have a TEMP_UNIT function? On the other hand you added some extra values. I assume these are the extra function of the SJB. What is "F-C"?

 As soon as I have the hole picture I can add a variant for the SJB model and the necessary command support via MQTT.

Monsardi, 2022-09-08:
F-C switches the display from fahrenheit to Celsius

jnsbyr, 2022-09-17:
@Monsardi
Thanks for your reply. So "F-C" is the same as "TEMP_UNIT" of the SBH - no big surprise here. That leaves the contradiction that your "TEMP_DOWN" has the same value.

Could you please answer all questions from my last comment in some detail? I do not have a SJB - so without you input I cannot make the required changes.

Monsardi, 2022-09-17:
Hi, i'm afraid I can't answer your other questions, as it is maceba96 who found out the rest of the code.

jnsbyr, 2022-09-17:
@Monsardi
Thanks for the quick feedback. Sorry I mixed up who had posted the codes originally. I still hope that @mabeca96 will add a comment.

jnsbyr, 2023-03-03:
@FireSale14

@mabeca96 has reported several codes that work with the SJB (see https://github.com/jnsbyr/esp8266-intexsbh20/issues/13#issuecomment-1194086643). So the hardware and the software of this project seem to be compatible. Now someone with an SJB needs to continue the code analysis, either with a logic analyser or by testing individual codes (see https://github.com/jnsbyr/esp8266-intexsbh20/issues/13#issuecomment-1183525195). 3rd alternative is to try reverse engineering the [DIYSCIP](https://github.com/YorffoeG/diyscip/) code.

Once this analysis is complete the support for the SJB can be added with a new configuration option. The coding could be done by me or can be provided as a merge request.

Please note that I am still unsure if finding the right codes is all it needs. With a working SJB and a logic analyser finding out is not that hard except for the wiring if you don't want to cut the display cable.

FireSale14, 2023-05-09:
@jnsbyr

Can you please help me? What hardware do I need? This? https://amzn.eu/d/cYtB7Zk? Which wires of the display should I connect it to? What should I press so that you can do something with it?
Thank you very much.

jnsbyr, 2023-05-09:
I will be happy to include anything you can find out. Maybe you need no logic analyser for this.

First look at [comment #13](https://github.com/jnsbyr/esp8266-intexsbh20/issues/13#issuecomment-1194086643). It already contains more than half of the solution. Use it as a starting point and confirm what @mabeca96 has documented.
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
algermi, 2023-05-30:
Servus Jens,

also erster Funktionstest abgeschlossen. Danke für's nachbessern des Scripts.

Model wird richtig erkannt. Intex PureSpa SJB-HS

pool/command/jet geht nur on, off geht nicht. 2. mal on senden, dann geht der Jet wieder aus, bei Bubble geht on/off.

pool/command/disinfection on, dann schaltet er auf 3 Stunden Desinfektion. Mehrmals "on" senden bringt keine Veränderung. Also aktuell keine Auswahl 3/5/8 Stunden.

Heater On/Off geht.

Filter On/Off geht

Mega Job, Geiler Schei... .

Mit Dir kann man arbeiten. :-)

algermi, 2023-05-30:
@jnsbyr

was ich gerade noch bemerkt habe, bei Filter=on, da schickt er anscheinend gleich wieder ein "off" hinterher.
Filter bleibt zwar an, aber im MQTT Server sehe ich folgenden Eintrag.
Weiss jetzt nicht ob das von Dir kommt, ich sehe auch im HomeKit, wenn ich den Schalter anschalte nur kurz on, dann springt der auf off.

May 30 15:59:25 raspberrypi homebridge[596]: [30.5.2023, 15:59:25] [Filter] Received MQTT: pool/filter = on
May 30 15:59:25 raspberrypi homebridge[596]: [30.5.2023, 15:59:25] [Filter] Received MQTT: pool/filter = off

jnsbyr, 2023-05-30:
@algermi

> Mit Dir kann man arbeiten.

Dito. Da ich kein SJB-HS habe und mir wohl auch keiner seins für die Entwicklung vorbeibringt, geht so zusammen trotzdem :-)

> ... bei Filter=on, da schickt er anscheinend gleich wieder ein "off" hinterher.

Habe noch einen Copy&Past-Bug gefunden, wo der Zustand der Desinfektion als Filterzustand gemeldet wurde. Neue Version 1.0.3.2 verfügbar. Wahrscheinlich ist das der Grund.

> Auch wenn ich den Heater anschalte, dann geht ja automatisch der Filter mit an ...

Das macht die Intex-Steuerung.

> ... das kann ich auch nicht erkennen im MQTT Client, da bleibt Filter auf Off.

Sollte eigentlich nicht so sein. Nimm die neue Version, schalte manuell am Display den Filter ein- und aus und beobachte, ob das per MQTT gemeldet wird.

> pool/command/jet geht nur on, off geht nicht. 2. mal on senden, dann geht der Jet wieder aus

Das kann ich leider nicht seblst nachvollziehen. Das erfolgreiche Umschalten hängt u.a. von der LED-Zuordnung ab. Schalte noch mal manuell am Display den Jet ein- und aus und beobachte, ob jede Änderung per MQTT gemeldet wird.

> pool/command/disinfection on, dann schaltet er auf 3 Stunden Desinfektion. Mehrmals "on" senden bringt keine Veränderung. Also aktuell keine Auswahl 3/5/8 Stunden.

Habe inzwischen einen möglichen Lösungsansatz, aber der ist relativ aufwendig. Würde gern erst die anderen Punkte oben alle abgefrühstückt haben. Du solltest die Zeit manuell am Display einstellen können. Bitte Info, ob sich die Intex-Steuerung beim Neustart der Desinfektion den zuletzt verwendeten Wert merkt oder z.B. immer 3 h vorschlägt.

algermi, 2023-05-30:
@jnsbyr

Servus,
ich werd morgen mal die neue Firmware testen, wie bereits erwähnt steht Dir mein SJB-HS gerne Remote zur Verfügung. Denke aber wir bekommen das final noch gelöst. Schönen Abend noch.

Lg Alex

algermi, 2023-05-31:
@jnsbyr

Moin Jens, also das mit dem Filter-Thema ist nun gefixt.

JET-Thema ist noch offen. Wenn ich per Display JET ON/OFF schalte, wir im MQTT sauber mit protokolliert. (pool/jet = on oder off)

wenn ich

pool/command/jet On/Off senden, da greift das Kommando (command) aber scheinbar wird der Topic Pool/JET nicht aktualisiert.

Zu diesem Thema:
(Bitte Info, ob sich die Intex-Steuerung beim Neustart der Desinfektion den zuletzt verwendeten Wert merkt oder z.B. immer 3 h vorschlägt.)

Beim drücken des Buttons Desinfektion wird immer als erstes der Wert 3 h vorgeschlagen, erneutes drücken des Buttons ändert dann auf 5 h und nochmaliges drücken auf 8 h.

algermi, 2023-06-01:
@jnsbyr

Moin, genau richtig, die Hoch/Runter-Buttons spielen für die Desinfektion keine Rolle.

Wenn der Desinfektionsbutton 4 mal hintereinander gedrückt wird ist die Desinfektion "wieder deaktiviert" d.h. das Desinfektionsprogramm startet nicht. Wenn das Desinfektionsprogramm z.B. 3 Stunden läuft und man es abschalten will, so muss man 4 mal drücken, läuft das Desinfektionsprogramm für 5 Stunden und soll beendet werden, dann muss man 3 mal drücken usw.

Die neue Version werde ich mir gleich mal testen und gebe dir wieder bescheid.

algermi, 2023-06-01:
@jnsbyr

Moin nochmal. Das Thema Jet ist Erld. on/off command funktioniert.

jnsbyr, 2023-06-01:
Super, danke fürs testen. 👍 Werde die aktuelle Version als "stabil" freigeben,

Mit deinen Rückmeldungen zur Bedienung der Desinfektion werde ich mir eine Lösung überlegen. Diese Erweiterung erfordert allerdings größere Umbaumaßnahmen an einer anderen Stelle, deshalb werde ich mir dafür ein paar Wochen Zeit nehmen.

algermi,
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

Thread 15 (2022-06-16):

Changing temperature not working reliably and may affect other settings

Profil404, 2022-06-16:
Hi,

All work except this: when I change the temperature, immediately after that the change take effect, the bubbles turn on. What I have to do to disable this comportement ?

Thank

jnsbyr, 2022-06-16:
The ESP application works more or less like web screen scraper - it interprets the output and presses buttons for you. So especially changing the temperature is quite a bit more difficult than turning bubbles on/off because reading and writing must be combined in a certain manner.

The ESP CPU by itself could do this easily but the ESP firmware regularly stops the application to service the WiFi client, otherwise the WiFi connection to the AP would be lost. This makes keeping the required microseconds timing for the pulses very difficult and takes the ESP to its upper limits. If the pulse timing is wrong something unintended can be affected.

Please check if you have build the project with the required CPU settings of 160 MHz. It this is already the case please report if it makes a difference if you change the temperature by only 1 degree.

Profil404, 2022-06-17:
C'est bien configuré à 160 MHz.

J'ai remarqué que ça arrive à chaque changement de température (même d'un seul degrés) mais également lorsque je met sous tension le module et le spa (par exemple après un reset électrique).

Via le moniteur série, à chaque fois que ça arrive je vois (de mémoire):

Dans bubbleOn
Testtest (plusieurs fois)
Fini

RealByron, 2022-06-17:
You should undefined Serial_debug. It can't be usable with blocking serial
debug in interrupts.
I'm investigating to robustify this interrupt. With my sb h20, this is the
temperature setpoint that can't be send on mqtt. I think that it we will
nicer to deal with frame with spi interrupt and press button timers.

Le ven. 17 juin 2022 à 08:34, Profil404 ***@***.***> a écrit :

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

jnsbyr, 2022-06-17:
@RealByron

Undefining Serial_debug can help, especially if you commented in the additional debug outputs in the source that log the received frames.

As I mentioned above, the temperature setpoint is the only critical/problematic thing I know of. If you plan to optimize you could start with _SBH20IO::setDesiredWaterTempCelsius()_ and _SBH20IO::changeWaterTemp_. E.g. there are several hardcoded parameters that affect the timing. Also take into consideration that the ISR and effectively _SBH20IO::decodeButton_ closes the control loop for changing the temperature setpoint and that the user request methods and the ISR influence each other and may run at the same time.

jybi89, 2022-06-19:
i have a same problem :'(
Publish to topic pool/command/water/tempSet ith mqtt explorer, so all functions start (bubble, on, off ect...)

jnsbyr, 2022-06-19:
@jybi89
Sorry to hear, but I see no way to "just" fix this problem, because there are too many variables. I optimized the original solution for my own SB-H20 and ESP8266. It does not work perfectly, but good enough for me, and it does not activate other functions. A small difference in you own ESP8266 hardware or in the pool firmware from Intex might be the cause, as not all users of this project seem to have this problem. There is also the possibility that the problem might be caused by the type or configuration of the MQTT server.

Only solution I see is that one of you with this problem tries to make changes to the ESP8266 firmware and see what happens. You can start with my hints to @RealByron above and I am willing to assist if there are questions.

I also suggest that before you change anything you should check what the MQTT server really sends to the ESP8266 when the MQTT server reconnects. You can use serial debugging for this on the ESP8266. As described in the Readme, the MQTT TCP connection gets interrupted when the water temperature is changed because the WiFi modem is put to sleep. Might be that your MQTT server sends the last set commands again.

piitaya, 2022-06-20:
Hi 🙂

The problem about the bubble is due to the `retain: true` flag you probably set to the command. You need to remove them and delete all the command topics using mqtt explorer or another tool.

Profil404, 2022-06-21:
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

Hi,

I don't have any `retain: true` when I send a command. And according to the HA documentation, by default retain is set t false. So yes, it's a firmware issue.

piitaya, 2022-06-21:
Or a wiring issue. I use it with HA for one month et zero issue on my side.

jnsbyr, 2022-06-21:
@Profil404
To make some headway, please try serial debugging:
- comment in "#define SERIAL_DEBUG" in common.h:33 and rebuild your firmware
- after firmware upload, start a terminal application (e.g. PuTTY) at 74880 baud
- look for output starting with "set ..." when sending a MQTT command (see MQTTClient.cpp:35ff)

RealByron, 2022-06-21:
I finally get all of this working. I will publish that on my fork project

Le mar. 21 juin 2022 à 22:46, Jens B. ***@***.***> a écrit :

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

RealByron, 2022-06-22:
Feel free to test my current investigation.
[test branch](https://github.com/RealByron/esp8266-intexsbh20/tree/optimizing)

Press button more robust
Temperature setpoint read fixed
publication on temps changes

jybi89, 2022-06-22:
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

ue mqtt explorer, may be a retain is here, delete the retain in mqtt explorer and test. I have solved my problem.

Profil404, 2022-06-22:
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

Already done, but I don't find any retain...

RealByron, 2022-06-23:
@Profil404 Did you checkout the "optimizing" branch ?

jnsbyr, 2022-06-23:
@Profil404
The output you posted looks quite unexpected. The "trying to connect to MQTT server ..." is from the default firmware but the rest must be from your own code because the firmware does output anything in French. It seems to me you did not activate the serial debugging successfully because the "set ..." output is missing that will be shown whenever a MQTT command is received. So please check line 33 in common.h again: it must start directly with "#define", not with "//#define". It the line looks good, the flashing probably did not work. Change the version in line 38 of common.h to another value and check via MQTT to be sure.

Closed 2023-05-30.

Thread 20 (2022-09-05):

Has anyone studied the possibility of connecting a solar panel ?

louis49, 2022-09-05:
I discovered that this spa consumes a lot of electricity and I would like to be able to partly heat the water with solar panels by adding them between the SPA and the pump (and thus use the pump through the solar panels).
Some questions :

- Do you think the pump can hold the style of assembling?
- Could a solenoid valve be added without consuming too much electricity (on 5v pin) and then allow the temperature to be limited to the maximum temperature of the SPA?
- Can solar panels allow to go near to the maximum temperature of the SPA? What gain is possible ?

Thank you

jnsbyr, 2022-09-07:
I assume you are talking about thermal panels and not electric panels.

> Do you think the pump can hold the style of assembling?

The pump is the weakest component of the SBH in respect to its power and power consumption. Adding thermal panels will probably reduce the water throughput further. The flow resistance might be found in the specs of the panels. If the smallest diameter of the pipe through the panels is not significantly smaller than that of the SBH you might get lucky but you will probably need an additional pump.

> Could a solenoid valve be added without consuming too much electricity (on 5v pin) and then allow the temperature to be limited to the maximum temperature of the SPA?

There is not much spare room inside the SBH pump case and it is even harder to add anything in a electrically safe way. But if you attach the solenoid in place of the electric heater you should have ample power at 230VAC. It is not a good idea to use a CPU pin from the mainboard directly. You would also need to modify the pipes of the SBH, probably on their way between the case and the pool. It should be easier to attach the valve outside the case.

> Can solar panels allow to go near to the maximum temperature of the SPA? What gain is possible ?

Thermal panels can produce very high temperatures, even above 100 °C. If you have very powerful panels I would not trust the temperature regulator of the SBH to do this safely. If you have panels with a power similar to the build in electric heater of the SBH it should not be a problem.

Note that I did not try this myself. Maybe someone with more experience can add a comment.

Closed 2023-02-05.

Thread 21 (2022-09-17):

Temperature sensor

louis49, 2022-09-17:
Hi,

I tried the temperature sensor part and discover 2 things :
* Accuracy is best when inverting voltage divider bridge (R1-R2)
* Consider that R1 has a 320k parallel resistance (made by an internal connexion between A0 and GND)

then, when computing temperature :

  ```
const int NTC_SAMPLES = 100;
const int NTC_PIN = A0;
const float NTC_BETA = 4300.f; // from https://cdn-reichelt.de/documents/datenblatt/B300/B57164K_ENG_TDS.pdf
const float NTC_VOLTAGE = 3.3f;
const float NTC_NOMINAL_RESISTANCE = 10000.f;
const float NTC_NOMINAL_TEMPERATURE = 25.f;
const float NTC_REF_RESISTANCE = 21600.f;
const float NTC_A0_RESISTANCE = 320000.f;

ADC_MODE(ADC_TOUT)

void setup() {
  Serial.begin(115200);
}

void loop() {
 float average = 0.0f;
  for (uint8_t i=0; i<NTC_SAMPLES; i++) {
    average += analogRead(NTC_PIN);
    delay(10);
  }

  float V_OUT = average / NTC_SAMPLES;
  V_OUT /= 1024;
  V_OUT *= NTC_VOLTAGE;

  float PAR_EQ = (NTC_REF_RESISTANCE*NTC_A0_RESISTANCE)/(NTC_REF_RESISTANCE+NTC_A0_RESISTANCE);
  float DIV_R2 = (V_OUT/NTC_VOLTAGE) * PAR_EQ/(1 - (V_OUT/NTC_VOLTAGE));

  float t_k = 1 / (
    (1.f / (NTC_NOMINAL_TEMPERATURE + 273.15f)) +
    (1.f / NTC_BETA) *
    (log(DIV_R2 / NTC_NOMINAL_RESISTANCE))
    );
    float t_c = t_k - 273.15f;

  LOG_D("V_OUT : %f ; Resistance : %f ; %f ; %f", V_OUT, PAR_EQ, DIV_R2, t_c);
}
```

Have you observed such a thing?

jnsbyr, 2022-09-17:
The temperature sensor in this project was an afterthought. I added it because it was easy and because it might be good to know how hot it gets inside an waterproof case - but accuracy was never a design goal here.

The Wemos D1 has an internal voltage divider at its analog input, so yes this will affect the mathematics for the temperature. The internal resistance (320 k) is higher by a factor of more than 10 in comparison to R2 (22 k). So this changes the effective resistance by less than 10 %. As mentioned before - accuracy was not important and the the initial accuracy of my setup was better than expected. If you follow the calibration procedure I described in the README.md it will not matter if you swap R1 and R2 or not.

If you want to go for higher accuracy you should also consider the following aspects:
- temperature range (equivalent to resistance range with a NTC as sensor)
- working point of your voltage divider (min/max voltage)
- accuracy of you ADC

You can optimize the resistor values and maybe switch R1 and R2, but with the ESP8266 you will loose at the 3rd point I mentioned above because of its 10 bit resolution. You can compensate this with high oversampling but some limits remain.

In another project of mine I added a ADS1115 to the Wemos D1, used a differential voltage measurement combined with a reference voltage auto calibration and the difference in accuracy in comparison to the build in ADC of the ESP8266 was really significant.

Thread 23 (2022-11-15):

no reaction to commands

swisscryptodev, 2022-11-15:
Hi
I love this project very much, but I don't get it fully working...
Everything works fine except the commands are not executed on the pool. After sending any command, there is no physical reaction of the pool. on MQTT the esp8266 sends an update of the old state.
In the attached example the filter is on and I send the command pool/command/filter off; but the filter stays on and the on the MQTT client we see the state update of the pool with pool/filter on.
Somehow the execution of the pressButton commands has no effect.

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

When I press the button on the pool panel, I get the correct state updates on the MQTT.

I have the SB-H20, WeMos D1 mini as ESP8266. Compiler settings are set as requested (160MHz, 4M, IRAM).

Any idea what could be wrong?

jnsbyr, 2022-11-16:
Sending commands to the SB-H20 is really tricky and takes the ESP8266 to its limits, at least in regard to the timing. Receiving the status updates is easy in comparison.

If you have access to a digiscope or a logic analyser you should connect it to the data line and see if the command pulses shown in the readme [diagram ](https://github.com/jnsbyr/esp8266-intexsbh20/blob/master/assets/Button-Signalling.png) appear when you send a command. Check before and behind the level shifter FET Q1.

If you do not have this kind of equipment it will not be easy. A mulitmeter will not be much help. Try checking if the FET pins are connected in the right order.

If the command pulses are not generated or generated at the wrong moment nothing happens at the SB-H20.

swisscryptodev, 2022-11-29:
Thanks, Jens for your answer.
I've found the problem. The issue was on the hardware side...: The soldering of the connection BS170, Pin2 to +3.3V was bad!!!
Now it works fine and as expected.
You can label this issue as "solved".
Very nice project! Thank you so much!

jnsbyr, 2022-11-29:
Thanks for your feedback swisscryptodev - enjoy!

Closed 2022-11-29.

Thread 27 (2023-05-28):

ESP Home installation failed.

RianFlow, 2023-05-28:
Hello. When installing on the wemos d1 mini, I keep getting errors. I've attached the log. maybe you can do something with it. Would appreciate any help.
[logs_esphome-web-819576_run.txt](https://github.com/jnsbyr/esp8266-intexsbh20/files/11583883/logs_esphome-web-819576_run.txt)

ESPHome 2023.5.4
INFO Reading configuration /config/esphome/esphome-web-819576.yaml...
INFO Generating C++ source...
INFO Compiling app...
Processing esphome-web-819576 (board: esp01_1m; framework: arduino; platform: platformio/espressif8266@3.2.0)
--------------------------------------------------------------------------------
HARDWARE: ESP8266 160MHz, 80KB RAM, 1MB Flash
Dependency Graph
|-- ESPAsyncTCP-esphome @ 1.2.3
|-- ESPAsyncWebServer-esphome @ 2.1.0
|   |-- ESPAsyncTCP-esphome @ 1.2.3
|   |-- Hash @ 1.0
|   |-- ESP8266WiFi @ 1.0
|-- DNSServer @ 1.1.1
|-- ESP8266WiFi @ 1.0
|-- ESP8266mDNS @ 1.2
|-- noise-c @ 0.1.4
|   |-- libsodium @ 1.10018.1
Compiling /data/esphome-web-819576/.pioenvs/esphome-web-819576/src/esphome/components/intexsbh20/SBH20IO.cpp.o
Compiling /data/esphome-web-819576/.pioenvs/esphome-web-819576/src/esphome/components/intexsbh20/SBHClimate.cpp.o
src/esphome/components/intexsbh20/SBH20IO.cpp:1:1: error: expected unqualified-id before '.' token
    1 | ../../../SBH20IO.cpp
      | ^
Compiling /data/esphome-web-819576/.pioenvs/esphome-web-819576/src/esphome/components/intexsbh20/intexsbh20.cpp.o
Compiling /data/esphome-web-819576/.pioenvs/esphome-web-819576/src/esphome/components/md5/md5.cpp.o
*** [/data/esphome-web-819576/.pioenvs/esphome-web-819576/src/esphome/components/intexsbh20/SBH20IO.cpp.o] Error 1
In file included from src/esphome/components/intexsbh20/intexsbh20.h:6,
                 from src/esphome/components/intexsbh20/intexsbh20.cpp:1:
src/esphome/components/intexsbh20/SBH20IO.h:1:1: error: expected unqualified-id before '.' token
    1 | ../../../SBH20IO.h
      | ^
In file included from src/esphome/components/intexsbh20/intexsbh20.cpp:2:
src/esphome/components/intexsbh20/SBHSwitch.h:10:77: error: 'IntexSBH20' was not declared in this scope
   10 | class SBHSwitch : public esphome::switch_::Switch, public esphome::Parented<IntexSBH20>
      |                                                                             ^~~~~~~~~~
src/esphome/components/intexsbh20/SBHSwitch.h:10:87: error: template argument 1 is invalid
   10 | class SBHSwitch : public esphome::switch_::Switch, public esphome::Parented<IntexSBH20>
      |                                                                                       ^
src/esphome/components/intexsbh20/SBHSwitch.h: In member function 'virtual void esphome::sbh20::SBHSwitch::write_state(bool)':
src/esphome/components/intexsbh20/SBHSwitch.h:27:4: error: 'get_parent' was not declared in this scope; did you mean 'get_name'?
   27 |    get_parent()->sbh()->setBubbleOn(state);
      |    ^~~~~~~~~~
      |    get_name
src/esphome/components/intexsbh20/SBHSwitch.h:31:4: error: 'get_parent' was not declared in this scope; did you mean 'get_name'?
   31 |    get_parent()->sbh()->setFilterOn(state);
      |    ^~~~~~~~~~
      |    get_name
src/esphome/components/intexsbh20/SBHSwitch.h:35:4: error: 'get_parent' was not declared in this scope; did you mean 'get_name'?
   35 |    get_parent()->sbh()->setPowerOn(state);
      |    ^~~~~~~~~~
      |    get_name
src/esphome/components/intexsbh20/SBHSwitch.h:43:7: error: 'get_parent' was not declared in this scope; did you mean 'get_name'?
   43 |   if (get_parent()->sbh()->isOnline())
      |       ^~~~~~~~~~
      |       get_name
In file included from src/esphome/components/intexsbh20/intexsbh20.h:6,
                 from src/esphome/components/intexsbh20/SBHClimate.h:4,
                 from src/esphome/components/intexsbh20/SBHClimate.cpp:1:
src/esphome/components/intexsbh20/SBH20IO.h:1:1: error: expected unqualified-id before '.' token
    1 | ../../../SBH20IO.h
      | ^
In file included from src/esphome/components/intexsbh20/SBHClimate.cpp:1:
src/esphome/components/intexsbh20/SBHClimate.h:9:95: error: 'IntexSBH20' is not a member of 'esphome::sbh20'
    9 | class SBHClimate : public esphome::climate::Climate, public esphome::Parented<esphome::sbh20::IntexSBH20>
      |                                                                                               ^~~~~~~~~~
src/esphome/components/intexsbh20/SBHClimate.h:9:105: error: template argument 1 is invalid
    9 | class SBHClimate : public esphome::climate::Climate, public esphome::Parented<esphome::sbh20::IntexSBH20>
      |                                                                                                         ^
src/esphome/components/intexsbh20/SBHClimate.cpp: In member function 'void esphome::sbh20::SBHClimate::update()':
src/esphome/components/intexsbh20/SBHClimate.cpp:8:2: error: 'SBH20IO' was not declared in this scope
    8 |  SBH20IO* sbh = get_parent()->sbh();
      |  ^~~~~~~
src/esphome/components/intexsbh20/SBHClimate.cpp:8:11: error: 'sbh' was not declared in this scope; did you mean 'sbh20'?
    8 |  SBH20IO* sbh = get_parent()->sbh();
      |           ^~~
      |           sbh20
src/esphome/components/intexsbh20/SBHClimate.cpp:8:17: error: 'get_parent' was not declared in this scope; did you mean 'get_name'?
    8 |  SBH20IO* sbh = get_parent()->sbh();
      |                 ^~~~~~~~~~
      |                 get_name
src/esphome/components/intexsbh20/SBHClimate.cpp:30:44: error: 'SBH20IO' is not a class, namespace, or enumeration
   30 |  this->target_temperature = (targetTemp != SBH20IO::UNDEF::USHORT) ? targetTemp : SBH20IO::WATER_TEMP::SET_MIN;
      |                                            ^~~~~~~
src/esphome/components/intexsbh20/SBHClimate.cpp:30:83: error: 'SBH20IO' is not a class, namespace, or enumeration
   30 |  this->target_temperature = (targetTemp != SBH20IO::UNDEF::USHORT) ? targetTemp : SBH20IO::WATER_TEMP::SET_MIN;
      |                                                                                   ^~~~~~~
src/esphome/components/intexsbh20/SBHClimate.cpp:32:20: error: 'SBH20IO' is not a class, namespace, or enumeration
   32 |  if (targetTemp == SBH20IO::UNDEF::USHORT)
      |                    ^~~~~~~
src/esphome/components/intexsbh20/SBHClimate.cpp: In member function 'virtual void esphome::sbh20::SBHClimate::control(const esphome::climate::ClimateCall&)':
src/esphome/components/intexsbh20/SBHClimate.cpp:46:3: error: 'get_parent' was not declared in this scope; did you mean 'get_name'?
   46 |   get_parent()->sbh()->setDesiredWaterTempCelsius(*tt);
      |   ^~~~~~~~~~
      |   get_name
src/esphome/components/intexsbh20/SBHClimate.cpp:52:3: error: 'get_parent' was not declared in this scope; did you mean 'get_name'?
   52 |   get_parent()->sbh()->setHeaterOn(*mode == climate::CLIMATE_MODE_HEAT);
      |   ^~~~~~~~~~
      |   get_name
src/esphome/components/intexsbh20/SBHClimate.cpp: In member function 'virtual esphome::climate::ClimateTraits esphome::sbh20::SBHClimate::traits()':
src/esphome/components/intexsbh20/SBHClimate.cpp:60:32: error: 'SBH20IO' has not been declared
   60 |  rv.set_visual_min_temperature(SBH20IO::WATER_TEMP::SET_MIN);
      |                                ^~~~~~~
src/esphome/components/intexsbh20/SBHClimate.cpp:61:32: error: 'SBH20IO' has not been declared
   61 |  rv.set_visual_max_temperature(SBH20IO::WATER_TEMP::SET_MAX);
      |                                ^~~~~~~
In file included from src/esphome/components/intexsbh20/intexsbh20.cpp:3:
src/esphome/components/intexsbh20/SBHClimate.h: At global scope:
src/esphome/components/intexsbh20/SBHClimate.h:9:95: error: 'IntexSBH20' is not a member of 'esphome::sbh20'
    9 | class SBHClimate : public esphome::climate::Climate, public esphome::Parented<esphome::sbh20::IntexSBH20>
      |                                                                                               ^~~~~~~~~~
src/esphome/components/intexsbh20/SBHClimate.h:9:105: error: template argument 1 is invalid
    9 | class SBHClimate : public esphome::climate::Climate, public esphome::Parented<esphome::sbh20::IntexSBH20>
      |                                                                                                         ^
src/esphome/components/intexsbh20/intexsbh20.cpp:8:6: error: 'IntexSBH20' has not been declared
    8 | void IntexSBH20::setup()
      |      ^~~~~~~~~~
src/esphome/components/intexsbh20/intexsbh20.cpp: In function 'void esphome::sbh20::setup()':
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
jnsbyr, 2023-05-28:
Can't help specifically as I do not have a ESPHome environment.

On first glance it looks like a Makefile/build related problem. It's always a good idea to start at the top:

> src/esphome/components/intexsbh20/SBH20IO.cpp:1:1: error: expected unqualified-id before '.' token
> 1 | ../../../SBH20IO.cpp
> | ^

I don't think that the 1st char on the first source line is the real problem here, as it should be "/*" (start of a comment) in SBH20IO.cpp. Looking closer you see the long relative path for the source file. As I don't have experience with ESPHome, I don't know if this is typical, but I would try to avoid this. What the error really seems to complain about is the "|". This is also not part of the source file, so it must be coming form somewhere else.

All other errors seem to have a similar pattern. So I suggest you check your build environment. Maybe there is someone who knows ESPHome who can offer more support.

RianFlow, 2023-05-29:
ok. Da ich kompletter Neuling auf diesem Gebiet bin, frag ich mich ob ich irgendwas an diesen Dateien ändern muss. An sich sind die Dateien ja leer. Und im Internet finde ich nichts dazu wie man so ein etwas größeres Projekt richtig auf den ESP bekommt. LG

OK. Since I'm a complete novice in this area, I'm wondering if I need to change anything in these files. The files are actually empty. And I can't find anything on the internet about how to properly get such a larger project on the ESP. LG

jnsbyr, 2023-05-29:
ESPHome is a platform of its own, in a way a competitor to Arduino. I assume that it might be possible to make the transition, but it could get hard, because the existing code uses interrupt service routines that must be kept in the RAM and not in the FLASH. These routines use almost all the RAM that is available on the ESP8266 so it might become difficult to make it work, if the platform itself also needs resources of that type. As the code is time critical even at 160 MHz, there is no alternative way to implement it without external hardware. Have a look at [diyscip](https://github.com/YorffoeG/diyscip) if you want to go that way.

If you hope that you might easily expand the current functionality with ESPHome, this might become difficult because of the same reason: The project needs almost all available RAM resources for its own purposes.

My advise: if you "just" want to make it work quickly, stay with Arduino firmware and do the interesting things like a web UI or remote control on the other side of the MQTT server with a smart home application.

RianFlow, 2023-05-29:
Ich habe jetzt versucht das ganze über Arduino zumachen. Hat soweit auch gut geklappt. Nur im Home Assistant finde ich nur den Temperatur zustand und den Device tracker. Muss ich noch irgendwas umbennenen?

I've now tried to close the whole thing via Arduino. Has worked well so far. I can only find the temperature status and the device tracker in the Home Assistant. Do I need to rename anything?

jnsbyr, 2023-05-29:
Wenn die Verbindung zwischen ESP und MQTT Server steht, solltest du in der Lage sein, alle vom ESP gemeldeten Topics zu empfangen (siehe [README/MQTT/Published Topics](https://github.com/jnsbyr/esp8266-intexsbh20#mqtt).

Vermutlich musst du jeden Topic einzeln mit einer Komponente im Home Assistent verknüpfen.

jnsbyr, 2023-08-04:
closed due to inactivity

Closed 2023-08-04.

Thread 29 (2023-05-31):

Homekit

louis49, 2023-05-31:
Hello!

I'm working on a HomeKit version but I've some trouble with tempset command that crash HomeKit part : [https://github.com/louis49/esp8266-intexsbh20/tree/homekit](https://github.com/louis49/esp8266-intexsbh20/tree/homekit). If someone can take a look ;-)
I'm using an adapted version of https://github.com/Mixiaoxiao/Arduino-HomeKit-ESP8266 that rename #define NO_INLINE because of a conflict with ArduinoJson

Waiting to find a solution, I published a homebridge plugin for interested people.

You can find it here : [https://www.npmjs.com/package/homebridge-intexsbh20](https://www.npmjs.com/package/homebridge-intexsbh20)

Have a good day

jnsbyr, 2023-05-31:
@louis49
If I understand the documentation correctly, HomeKit is an alternative to MQTT. It's certainly possible to run it in parallel, but the ESP8266 MCU is not that powerful, so I would opt for a feature selection in *common.h* using a *#define UPLINK_HOMEKIT* (or similar) that excludes the MQTT parts when enabled. This would free up some RAM/FLASH resources and maybe help with your crash.

As the HomeKit library also requires a 160 MHz this might be a problem. The current code enables and disables WiFi when changing any settings, especially the temperature, see *[SBH20IO.cpp](https://github.com/louis49/esp8266-intexsbh20/blob/homekit/SBH20IO.cpp)*, because otherwise the pulse-timing has too much jitter and the Intex controller will not react as expected. I am not sure that another library that relies on a WiFi connection will be happy about this. The MQTT connection is also interrupted during that time, but re-establishes immediately after the action is completed. It might be necessary to explicitly pause the HomeKit connection during the time critical phase when the WiFi is down or to revive it after the WiFi is back.

A second step regarding clean code may be to implement a new class that handles the required abstraction so that the main code does not need to be changed every time a change for MQTT or HomeKit is needed. Problem here is that the ISRs in *SBH20IO.cpp* must stay in RAM and their size is already at the upper limit.

louis49, 2023-06-01:
Ok, I'll try disabling MQTT, but I'm not far from thinking that it will be essential for me to switch to an ESP32 to complete this project. At worst I have the HomeBridge solution which does the job. It's really a great job this project in any case, it works really very well: congratulations!

jnsbyr, 2023-06-01:
Was thinking in the same direction. The resources and restrictions of the ESP8266 may not be enough to handle both the Intex IO and the HomeKit IO, so switching to the ESP32 may do the trick. You probably know that there are several ESP32 versions around (S1, C3, ...). They all seem more powerful than the ESP8266, but the later versions have a completely different CPU core and behave differently and use a little less energy than the earlier ones. Will need some testing to find the perfect match.

louis49, 2023-06-02:
Finally I managed to make everything work last night: indeed the Wifi disconnection was the cause - there was a bug in the Homekit library that I was using when the Wifi was cut, the connection with HomeKit was cut. I created the necessary branch and added the fix on compatibility with ArduinoJson [https://github.com/louis49/Arduino-HomeKit-ESP8266](https://github.com/louis49/Arduino-HomeKit-ESP8266)

It seems to work in parallel with MQTT without any problem: do you want me to create a feature selection based on #define anyway?

Can we limit ourselves to this correction or do you want me to move forward on the element of CleanCode mentioned to accept my next Pull Request?

jnsbyr, 2023-06-02:
As most users do not need to uplinks, the required uplink should be selectable in a way. With a define the project needs:

- less resources (RAM, flash)
- less dependencies to other libraries, allowing easier build

This may provide a user room for individual extensions and it simplifies the build as the user does not need to download all possible dependencies.

Bringing MQTT and HomeKit support together in one project should be an advantage to the users. The following things need to be done from my point of view:

- Your code needs to be updated to the latest version that also supports the Intext PureSpa SJB-HS model. For this I had to rename the class SBH20IO to PureSpaIO. The new model has 2 additional functions corresponding to 4 new MQTT topics (jet, disinfection). The disinfection time can be selected and read back, but this is not jet supported as it needs a significant rework of the display decoding. This is something I plan to do in the near future.
- Please add the defines to support building for MQTT, HomeKit or both. The defines should also be used to remove all unneeded external dependencies when not active by not including them. Default should be either both MQTT and HomeKit off + #error directive (similar to the new model selection).
- Next I will update the README to describe the support for the new model SJB-HS. When adding the HomeKit support another rewrite is needed and for this your input is required. The aspects to cover are a) feature description, b) build specifics and c) configuration/usage. These aspects could be added to the current README. But it is already getting long, so I am thinking about splitting it in several parts first, e.g. a) general b) hardware c) MQTT d) HomeKit. We can address this after the merge is done.
- For the merging I will create a feature branch "homekit". Once this version looks good to both of us we can merge to the main branch.
- If you agree, I would add you as collaborator to the project after the initial merge, so that there is no need to for me to validate every change you might deem necessary in the future. Only condition here is that you do not make "random" changes to the code and try to respond to issues that are HomeKit related when you have the time.

Elektroarzt, 2023-06-22:
@louis49
I flashed your HomeKit solution from [GitHub](https://github.com/louis49/esp8266-intexsbh20/tree/homekit) and find it really awesome to have HomeKit functionality in this tiny device! My understanding is to flash your project after installing 'HomeKit-ESP8266' from Mixiaoxiao in Arduino IDE.
The HomeKit devices then appear properly in the HomeKit App but they seem to be not responding regularly. As I have the MQTT path in parallel running and this is responding, I can exclude my network environment as the root cause. Do you experience the same issue or did I do something wrong in building the project?

jnsbyr, 2023-08-04:
closed due to inactivity

Closed 2023-08-04.

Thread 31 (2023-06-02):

BOM and CPL files

thombrink, 2023-06-02:
Can you export the BOM and CPL from the Pool SB-H20 WiFi MQTT.fzz file and/or add to the repo? I've installed fritzing but cant find an option to export those files.

Elektroarzt, 2023-06-02:
Fritzing is a lab tool from my point of view. I opened fritzing with the project and didn't find any option therefor, too. I don’t use Fritzing usually, as this project was just a test. I'm using KiCAD.
As there are just few components, it is straight forward to read the values out of the [schematic](https://github.com/jnsbyr/esp8266-intexsbh20/blob/master/assets/Schematic.png) of jnsbyr. The placement of the components can be read from the silkscreen print on the PCB, so there is no need for a CPL file.

thombrink, 2023-06-02:
Ah I understand. The reason I asked is because I'm a software developer and don't have any low voltage components knowledge. So my idea was to just let jcbplc place the components for me instead, but they asked for those files.

In the meantime I've found someone who's willing to help me sort out the required components and help me place and solder the correctly.

Thanks for the schematics image, I missed that one!

Elektroarzt, 2023-06-02:
Ok, sounds good to jump in the hardware a bit :). Maybe the hurdle for the next steps after having the right components is high, if you do not have the knowledge of sealing the PCB in terms of IP protection and connecting to the bus cable. Please let me know if I can help you with a plug-and-play hardware solution I 3D printed.

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

thombrink, 2023-06-02:
Haha so it seems ;) I do have experience sealing 230v wiring, but your solution looks awesome! If you would like to share the print files for those components, that would be great!

You already saved me a lot of thinking time on what should be the best position of the box :)

Elektroarzt, 2023-06-02:
I thought of publishing the files at printables.com ... this would be the right place I think with a link to this GitHub page. If you like to have a ready assembled unit, mail me at elektroarzt@digital-filestore.de
For publishing the files it takes a bit of work from my side, please give me some time. Otherwise there will be more questions than answers just kicking out the files without comment or any guidance how to use it.

thombrink, 2023-06-02:
No problem! It's a hobby project and it will take a while before the pcb will arrive. However, if I somehow can't get it all working, then I will send you an email!

I'm also thinking about creating a mobile app instead of using HA. Although I haven't decided yet if I will publish it to the store. That depends on whether there is enough interest. Otherwise I will make a separate apk and ipa available.

Thanks sor far!

SpaWnOL68, 2023-06-10:
Hello. Is it possible to have this BOM files? I would like to let JLPCB do the soldering and it requires this files. Thanks

thombrink, 2023-06-10:
Please read the first response of @Elektroarzt he already answered that question I guess.

SpaWnOL68, 2023-06-10:
I read it but i am not really sure about  the exact componant needed for this project.

SpaWnOL68, 2023-06-10:
> I read it but i am not really sure about the exact componant needed for this project. If maybe someone could give more detail I am really interested.

Elektroarzt, 2023-06-11:
I could provide a short BOM with links for e.g. Conrad in Germany. But it always depends on where you live and where you source your components. Be aware ... if you are not familiar with electronics design, it could be really dangerous to modify a pool which is powered by 230V. Remember, you may have children in the pool and in the worst case water everywhere, not only in the pool. If you are not sure, what you are doing, the risk could be too high.
A proposal ... do you have a friend with electronics background who is willing to help mounting everything together? He will know where to source the needed standard components and how to securely modify the pool.

If you anyway insist on the partslist, let me know.

SpaWnOL68, 2023-06-11:
I agree and I don't want to take any risk of course. I know some guy who can do it and I think I am able to follow the Electric schematic. But we cannot buy this project right ? Are you able to help in doing it ? Thanks

Elektroarzt, 2023-06-11:
I could provide the solution you see on the pictures above for self cost. But this is only for SB-H20, as I just have this model. From the MQTT broker you would have to go your own way, because the software is typically very individual, depending on the HA software you use (ioBroker, HASS, Node Red, etc.). The project is not plug-and-play at the moment.
If you like to go that way, leave PN under elektroarzt@digital-filestore.de

SpaWnOL68, 2023-06-11:
Thanks. I have sent you an email.

Elektroarzt, 2023-06-12:
I did not receive your email, sorry

SpaWnOL68, 2023-06-12:
> I did not receive your email, sorry

Maybe in your spam. I have sent you another one.

B4n4n3, 2023-06-15:
Hey @Elektroarzt i have sent you a email on the Weekend too, but i think you dont received it. Maybe Something wrong with your Mail-Server?

thombrink, 2023-06-15:
I don't want to get pushy, but how is the cleanup process going @Elektroarzt? If you haven't had the time to clean up the print file(s) then its no problem to just send/upload them as they are. A friend of mine has a lot of experience with 3d printing and asked me the stl file. I won't bother you if we somehow can't understand the file/drawing.

Thanks in advance!

Elektroarzt, 2023-06-15:
I like to make a short how-to, it's not about cleaning up the models. There will be questions about the contacts to use, how to insert them, the housing and the support that is needed for the print, material and so on. If I kick out the files, I'm sure many people will ask the same questions.
I'm on holiday until Sunday, so next week I will publish the files including sources of the components once WiFi is back in my life.

Elektroarzt, 2023-06-15:
> Maybe Something wrong with your Mail-Server?

Mail slipped in my spam, sorry. Answer goes out.

thombrink, 2023-06-15:
Ah I understand! Enjoy the rest of your holiday and thanks for the work you've done so far!

Elektroarzt, 2023-06-16:
@jnsbyr: I would publish the files and the how-to for the above mechanical solution on printables.com as there is a built-in 3D-Viewer for the uploaded models and it is the main starting point in the 3D printer community. Do you agree? If you have a good idea for linking in to this project, please let me know. Otherwise I would refer to your GitHub page and keep the information there reduced on the mechanics to avoid doubles on both sides. Maybe a link from here to printables.com would then be ideal.

Elektroarzt, 2023-06-20:
The files are published on [Printables.com](https://www.printables.com/de/model/509289-intex-purespa-whirlpool-controller-mechanics)
@jnsbyr: Please check for linking in both directions. If you need something, please let me know.

jnsbyr, 2023-06-21:
@Elektroarzt
Have rewritten the [Case & Co.](https://github.com/jnsbyr/esp8266-intexsbh20/blob/master/README.md#case-cables-and-connectors) paragraph of the README. It now includes a short description of your project and a link.

Please let me know if you have additional info that should be added.

I think this should complete this issue. If you agree, please close it.

Elektroarzt, 2023-06-22:
Fits for me, thanks!

Closed 2023-06-22.

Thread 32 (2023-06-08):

arduino flash ESP error

Matze5593, 2023-06-08:
Hello, when I want to flash the ESP D1, I get the following error message:

C:\Users\XxX\Desktop\esp8266-intexsbh20-1.0.3.3\esp8266-intexsbh20\esp8266-intexsbh20.ino: In function 'void setup()':
esp8266-intexsbh20:145:31: error: exception handling disabled, use -fexceptions to enable
     catch (std::runtime_error re)
                               ^
esp8266-intexsbh20:147:22: error: 're' was not declared in this scope
       Serial.println(re.what());
                      ^
exit status 1
exception handling disabled, use -fexceptions to enable

louis49, 2023-06-08:
You need to activate exceptions handling in your Arduino IDE

Matze5593, 2023-06-08:
ok i did it it works.

in the config.json we use the mqtt server "mqttServer": "mqtt.at.home",

set. Is this in the ESP or do you have to enter the IP address of an existing Mosquitto broker here

Closed 2023-06-08.

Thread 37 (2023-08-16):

Communicate with arduino

fitorie, 2023-08-16:
Dear Sir,

Thanks for sharing your project. It is very interesting.

I expose my issue:

My solar inverter closes a relay when reaching some photovoltaic sun irradiance parameters.
I want to turn on the Intex spa heater when that relay is closed to derive photovoltaic power excedents to heat the spa.

My problem is that the inverter is 12 meters away from the spa and I don't have wired cable from one to another.
My first idea was to pair 2 arduino using RF 433 Mhz (one in each side) and modify your code in the arduino that controls the ESP8266 in order to turn on heater when the first arduino detects solar inverter relay closed.

However, I wonder if a simpler solution using MQQT or Home Assistant is possible.

Any help is much apreciated.

Thank you very much in advance
Kind regards from Spain

jnsbyr, 2023-08-16:
This is a DIY project for controlling specific PureSpa models. It describes a possible solution (hardware and software) if you have the expertise to manufacture it yourself. It is not a ready to use commercial solution and there is no how-to that describes how to proceed in detail.

I am sure there are commercial relay units available that can be used with Home Assistant and an external heater unit. But if you are talking about the heater in the PureSpa box, then things become dangerous. I can only discourage you from proceeding if you are not an professional electrician or if you do not intend to let a professional electrician plan and execute any modifications. The heater uses mains voltage and even though there is an RCD attached to the PureSpa an unqualified modification can still cost lives.

jnsbyr, 2023-08-22:
closed due to inactivity

Closed 2023-08-22.

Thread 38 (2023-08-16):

Simplify PCB

fitorie, 2023-08-16:
To simplify soldering PCB, is it possible to use a board level shifter and the capacitor?
The guy here: https://github.com/RealByron/PicoW-Intex-PureSpa only uses capacitor and commercial level shifter to connect to a Raspberry pico W.
Obviously the board would not be so robust but without termometer, fusible and using commercial board that act as level shifter, things become easier.

I understand this should be possible with Wemos D1

Please confirm if this is possible.

Thanks a million.

jnsbyr, 2023-08-16:
Often there are many ways to achieve a certain goal. But a commercial PCB is not a strict requirement - it just makes things easier to reproduce, once a final design is available.

> ... is it possible to use a board level shifter and the capacitor?

Yes.

jnsbyr, 2023-08-22:
closed due to inactivity

Closed 2023-08-22.

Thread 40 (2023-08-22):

Desired temperature regressions

kvj, 2023-08-22:
Hi,

First, thanks a lot the great work on the project!

While playing with the latest release 1.0.8.0, I've discovered few issues:
* Desired temperature field is always empty, it seems like blinking detection code is failing.
* Up/Down buttons aren't being triggered, not by using `setDesiredWaterTempCelsius()` method, not by calling `changeWaterTemp()` directly

I'm having `MODEL_SB_H20` pool.

jnsbyr, 2023-08-22:
I did not perform a runtime test with firmware 1.0.8.0 before, but I tried it a few minutes ago and it is working for me, as did the previous firmware 1.0.7.2.

Please let me know:

- which was the last firmware version you used that worked for you
- what build system you are using (Arduino, vsCode + Arduino CLI, PlatformIO, etc.)
- what library and SDK versions have been used by the build (look for the summary output at the end of the build process)
- does the display start to blink when changing the desired temperature
- do any other commands work (e.g. power on/off)

kvj, 2023-08-23:
> which was the last firmware version you used that worked for you

Not sure I remember did I test the temperature change or not. But at least other basic functions worked.

> what build system you are using (Arduino, vsCode + Arduino CLI, PlatformIO, etc.)

VSCode + Platformio 6.10.0

> what library and SDK versions have been used by the build (look for the summary output at the end of the build process)

```
PACKAGES:
 - framework-arduinoespressif8266 @ 3.30102.0 (3.1.2)
 - tool-esptool @ 1.413.0 (4.13)
 - tool-esptoolpy @ 1.30000.201119 (3.0.0)
 - toolchain-xtensa @ 2.100300.220621 (10.3.0)
```

I guess here [1] you have a typo, `framework-arduinoespressif8266@3.30102.0` doesn't belong to the `board_build.filesystem` key

[1] https://github.com/jnsbyr/esp8266-intexsbh20/blob/13542c1907572546c26eea5fcef0babc380b40bd/platformio.ini#L20

> does the display start to blink when changing the desired temperature

Nope. Both buttons (Up/Down) aren't being triggered, so also no buzzer.

> do any other commands work (e.g. power on/off)

Other buttons work as expected: Power, Filter, Bubble, Heater. Sometimes from the second attempt, but quite reliable still

jnsbyr, 2023-08-24:
> Not sure I remember did I test the temperature change or not. But at least other basic functions worked.

As I do not have access to your hardware and cannot reproduce the issue with my hardware this is a very crucial aspect to help narrow down a possible cause. Please build and test the previous releases until you find the one that is working for you. But try test described below first.

>framework-arduinoespressif8266@3.30102.0 doesn't belong to the board_build.filesystem key

Thanks, that's a copy&past bug. Should look like this:

```
platform_packages =
   framework-arduinoespressif8266@3.30102.0
```

> Both buttons (Up/Down) aren't being triggered ... Other buttons work as expected

Please increase the int value 380 for PRESS_SHORT_COUNT in PureSpaIO.h:238 to a higher value, e.g. in steps of 10 until it works or until you have reached 500.

kvj, 2023-08-28:
> Please increase the int value 380 for PRESS_SHORT_COUNT in PureSpaIO.h:238 to a higher value, e.g. in steps of 10 until it works or until you have reached 500

I've tried few options over the weekend, and nothing worked:

1. I've increased `PRESS_SHORT_COUNT` few times up until `PRESS_COUNT` value
2. I've also tried to trigger Up/Down buttons using the `set<Whatever>On()` logic, with the respective button values

The desired temperature isn't being detected if I manually press Up/Down buttons. The screen blinks with new value but the variable stays undefined

jnsbyr, 2023-08-28:
Sorry to hear that you made no progress. As I cannot reproduce your issue, please try to find out which was the last firmware version that did work for you.

Vrumfondel, 2023-10-01:
Hi there,
I'm experiencing similar issues like kvj: With  1.0.8.1 controlling is not working at all for me, while with 1.0.7.2 it works quite decent.
With neither of the versions I receive the topics pool/water/tempAct and pool/water/tempSet.

jnsbyr, 2024-05-25:
I just repeated a tests with

- release 1.0.8.1
- SB-H20 model
- SERIAL_DEBUG disabled
- FORCE_WIFI_SLEEP disabled

I cannot find any issues with my setup. tempAct and tempSet are correct in MQTT and follow any changes on the SB-H20 immediately. Changing tempSet via MQTT also works.

If you haven't already tried: enable FORCE_WIFI_SLEEP with release 1.0.8.1 as it will provide the control behaviour of the previous releases with the disadvantage that MQTT connection gets lost when changing the temperature setpoint and the advantage of a more robust pulse timing. The main problem here is the design of the ESP8266 as the WiFi protocol is handled by the CPU, interrupting the application code anytime. On would need to upgrade to a ESP32S3 to have a CPU core just for the application - not sure if this is worth the necessary code migration.

It might be that the clock speed of the connection between pool mainboard and pool display vary from model to model or by production date or whatever. Significantly different clock speeds will require different pulse timings, independently of the question about ESP8266 and WiFi modem sleep. But with only a single device available to me I have no way to find cause and solution by myself. One option to start would be to measure and compare the display clock frequencies. The README.md specifies the nominal clock frequency as 100 kHz and shows a plot of more than 300 µs -  this can be used as a reference for any comparisons.

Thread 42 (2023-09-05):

Feature Request: Adapt to ESP32

Vrumfondel, 2023-09-05:
Adapting to an ESP32 environment would have the advantage of a multi-core ECU, so the time-critical interfacing part could run on a seperate ECU, while all the WIFI and UI stuff runns on the other.

jnsbyr, 2023-09-08:
No doubt, but it will:

- increase the costs per board
- probably increase power consumption

Also: the additional CPU power of an ESP32 is not needed for a pure MQTT gateway. Only when you want to run a webserver on the chip things start to look different. But if you have MQTT you will also have a smarthome. So why have another webserver on the chip? But I don't want a discussion about this here.

There are several forks of this project available for more powerful hardware including ESP32 and Raspberry Pi Pico W. Take a look at the closed issues and at https://github.com/jnsbyr/esp8266-intexsbh20/network and you will be able to find them.

A while back I tried to motivate the authors of these forks to help create a new combined firmware version that supports several hardware platforms at the same time, but there was no response. I will not start an this path on my own as this is a fun project for me and it should stay that way. But if there is someone willing to put time into this idea I will support it.

Vrumfondel, 2023-09-09:
Hello,
thanks for the answer.
1. Price increase: Yes, the price for the ESP board would incrase from 1.84€ to 3.97€. Honestly, not a really big jump.

2. Powerconsumption. This is true aswell, the powerconsumption of an ESP32 is higher then the 8266. On the other hand: We are talking about a device which heats  some 100l of water electically, so this is not really counting in my opinion.

Finally I would keep the project anyways flexible for the user to choos the variant, so everyone can choose what he prefers.

I'll have a look to the other projects.

jnsbyr, 2023-09-09:
> Finally I would keep the project anyways flexible for the user to choos the variant, so everyone can choose what he prefers.

No limitations intended from my side. This is a public repo, anyone can fork and mod.

Please note: When a project has more than a handful of technologically involved users, the project must work reliably for anyone, at least for a defined set of parameters. If you try to support several hardware platforms and IDEs, you, as project maintainer, either know your way around all these and perform regular tests with all these, or you will get quickly swamped with support requests where this or that combination does not work. This typically requires manpower to handle and this project currently does not have the necessary number of volunteers to do more. Have a look [CONTRIBUTING.md](https://github.com/jnsbyr/esp8266-intexsbh20/blob/master/CONTRIBUTING.md) if you want to help.

jnsbyr, 2024-05-25:
closed due to inactivity

Closed 2024-05-25.

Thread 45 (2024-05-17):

Cant bring it to work

cyclemat, 2024-05-17:
have tried to compile aover arduino IDE 1.8 and platform IO
on PIO i bacome an error Tasmota 8266 not avaible

so ich change the platformio.ini
[env:d1_mini]
board = d1_mini
board_build.f_cpu = 160000000L
board_build.filesystem = littlefs
build_flags =
	-D PIO_FRAMEWORK_ARDUINO_LWIP2_LOW_MEMORY
	-D PIO_FRAMEWORK_ARDUINO_ENABLE_EXCEPTIONS
	-D VTABLES_IN_IRAM
platform = https://github.com/platformio/platform-espressif8266.git
platform_packages =
   framework-arduinoespressif8266@3.30102.0
monitor_speed = 74880

it build but didnt work no ip adress in my network and no mqtt messages . the  can anybody  help me ?

jnsbyr, 2024-05-18:
More information is required to pin down the problem.

- your platformio.ini looks good
- check in the logs of your WiFi access point and your DHCP server for any activity of the esp8266
- enable SERIAL_DEBUG in common.h, rebuild, and use the serial monitor at 74880 baud - if the output does not help you to resolve the problem by yourself, post it
- Did you upload the config file to the esp8286? If yes, post your config with the secrets anonymized.
- Which firmware version did you use?

cyclemat, 2024-05-18:
No Activity on my DHCP or on the WiFi No unknown device.
 will try to enable debug in the next days
Yes have Upload the config File.
Upload this after the Weekend. Give IT Problems with space in the ssid ?
Have used the newest Upload with the copiler Error fix.

cyclemat, 2024-05-19:
chksum 0x2e
load 0x3fff20b8, len 40, room 8
tail 0
chksum 0x2b
csum 0x2b
v00066830
~ld
error: pll_cal exceeds 2ms!!!
rf cal sector: 1020
freq trace enable 0
rf[112] : 0⸮Intex PureSpa SB-H20 MQTT WiFi Controller 1.0.8.1
build with Arduino Core for ESP8266 3.1.2
based on Espressif NONOS SDK 2.2.2-dev(38a443e)
config file loaded successfully (has 9 entries)
required entry 'CyCleMat IOT' not found in config file

cyclemat, 2024-05-19:
{
 "wifiSSID":       "CyCleMat IOT",
 "wifiPassphrase": "xxxxxxxxxxxxxx",
 "mqttServer":     "192.168.0.200",
 "mqttPort":       "1883",
 "mqttUser":       "xxxxxxxx",
 "mqttPassword":   "xxxxxxx",
 "mqttRetain":     "YES",
 "firmwareURL":    "",
 "errorLanguage":  "EN"
}

Elektroarzt, 2024-05-19:
Is it possible you modified the source code with your WiFi credentials as well?
The debug log shows "required entry 'CyCleMat IOT' not found in config file", as if the main code searches for this string in the config file!?

cyclemat, 2024-05-19:
my failure had understand that i need to input the config in the common.h sorry im stupid :)

Elektroarzt, 2024-05-19:
Just choose your pool type in the common.h and edit the config to your needs and it should work

Closed 2024-05-19.

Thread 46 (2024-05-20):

Pool topics changes continuously

marcosgar, 2024-05-20:
Hi
First of all thanks for the great job and detailed description.

I have built the PCB following the provided schematics and programmed the ESP8266 using PlatformIO IDE.

Once the board was connected to my SPA, it connected correctly to my WiFi and through MQTT Explorer I was able to see the status topics of the pool. The problem I have is that the topics power, bubble and filter constantly change between on and off and it does not reflect the real state of the SPA. The temperature does show correctly and I have managed to activate the bubbles from my PC after many attempts.

Has this ever happened to you? Do you have any idea what could be the reason why the topics are not received well or that they constantly change?

Thanks in advance

jnsbyr, 2024-05-20:
The pool topics are updated every 10 s, but they should not toggle randomly. Here are some hints how to analyse:

- Rebuild the code with SERIAL_DEBUG enabled in common.h. Maybe add a few extra log outputs, e.g. to MQTTPublisher::loop(), so you can see what values are really provided by the device. Let the debug version run for a short while and watch what happens in your MQTT client and in the serial output at the same time. Note that serial debugging reduces the application stability, so do not be surprised if some things behave even worse (e.g. giving commands) - but it is the easiest way to look deeper into the application.

- Alternatively use something like tcpdump or Wireshark to look into the connection from the device to your MQTT broker. MQTT Explorer is a MQTT client and can only see what the MQTT broker provides. It could be an issue of the MQTT broker setup.

jnsbyr, 2024-05-25:
closed due to inactivity

Closed 2024-05-25.

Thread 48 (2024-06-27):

Panel buttons not working with Wi-Fi controller plugged in

Giuse235, 2024-06-27:
Hi, I followed the electrical scheme and the device is working fine and I'm able to control everything via MQTT but whenever the controller is plugged to the pool panel, I'm not able to control the pool using phisical buttons anymore.
I noticed that if I disconnect the DATA pin to the panel, it works again. Can you help me? Thanks

Elektroarzt, 2024-06-27:
Hi ... did you check your level shifter around MOSFET Q1 in terms of pinning and wiring? You could test the function isolated on your workbench if the level is properly shifted between 3.3V and 5V.

Giuse235, 2024-06-27:
I have a doubt that my MOSFET may be reversed (drain and source switched)... May this be the problem? What is the correct wiring for the MOSFET? Can you please tell my how to check it on the workbench? What do you mean with "if the level is properly shifted between 3.3V and 5V"? Thank you

Elektroarzt, 2024-06-27:
Please read this tutorial concerning level shifting utilizing BS170:

https://www.digikey.com/en/blog/logic-level-shifting-basics

You can measure the reverse diode of the MOSFET with a simple multimeter to check the correct orientation of the pins. If it shows around 0.7V, you measure the diode in forward direction.

jnsbyr, 2024-10-26:
closed due to inactivity

Closed 2024-10-26.

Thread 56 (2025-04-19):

Color Code for Data/Clock/Latch Wires ?

CaptnRamius, 2025-04-19:
First of all, thanks to everybody who has contributed to this great project, it sounds fantastic !
I own an Intex PureSpa SB-H20 and I have implemented all the modifications (exactly trying to copy Jens' hardware solution from the ) but I am having trouble obtaining good values from the tapped pool control unit.

My first problem is that I am not 100% sure anymore, whether I connected the input wires correctly, i.e. which are the data, the clock and which one is the latch (the ESP starts up, so I think I have identified 5V and ground correctly ;-) ).
**Does anybody have the color code for the SB-H20 cable that connects the control unit to the pump/heater ?**

Funnily, yesterday, when I started soldering things, Jens' link for 3D printing (main project page) to the Intex PureSpa connector on thingiverse had still worked, and I remember that CAD drawing showed some color codes. But that link is not working any longer (I guess it has expired today after 6 months?): [Intex PureSpa connectors](https://www.thingiverse.com/thing:4130911)

I have set up a small Mosquitto server to receive messages. In the best configuration so far I am receiving all of the messages below within a few seconds, which seems to be way too many:

> Client mosq_sub1 received PUBLISH (d0, q0, r1, m0, 'wifi/state', ... (7 bytes))
offline
Client mosq_sub1 received PUBLISH (d0, q0, r1, m0, 'wifi/ip', ... (13 bytes))
192.168.xx.yy
Client mosq_sub1 received PUBLISH (d0, q0, r1, m0, 'wifi/version', ... (7 bytes))
1.0.8.2
Client mosq_sub1 received PUBLISH (d0, q0, r1, m0, 'pool/model', ... (20 bytes))
Intex PureSpa SB-H20
Client mosq_sub1 received PUBLISH (d0, q0, r0, m0, 'pool/bubble', ... (3 bytes))
off
Client mosq_sub1 received PUBLISH (d0, q0, r0, m0, 'pool/filter', ... (2 bytes))
on
Client mosq_sub1 received PUBLISH (d0, q0, r0, m0, 'pool/power', ... (3 bytes))
off
Client mosq_sub1 received PUBLISH (d0, q0, r0, m0, 'pool/heater', ... (7 bytes))
standby
Client mosq_sub1 received PUBLISH (d0, q0, r0, m0, 'pool/water/tempAct', ... (2 bytes))
36
Client mosq_sub1 received PUBLISH (d0, q0, r0, m0, 'pool/water/tempSet', ... (3 bytes))
-99
Client mosq_sub1 received PUBLISH (d0, q0, r0, m0, 'wifi/state', ... (6 bytes))
online
Client mosq_sub1 received PUBLISH (d0, q0, r0, m0, 'pool/error', ... (0 bytes))
Client mosq_sub1 received PUBLISH (d0, q0, r0, m0, 'pool/filter', ... (3 bytes))
off
Client mosq_sub1 received PUBLISH (d0, q0, r0, m0, 'pool/heater', ... (3 bytes))
off
Client mosq_sub1 received PUBLISH (d0, q0, r0, m0, 'pool/filter', ... (2 bytes))
on
Client mosq_sub1 received PUBLISH (d0, q0, r0, m0, 'pool/heater', ... (7 bytes))
standby
Client mosq_sub1 received PUBLISH (d0, q0, r0, m0, 'pool/filter', ... (3 bytes))
off
Client mosq_sub1 received PUBLISH (d0, q0, r0, m0, 'pool/heater', ... (3 bytes))
off
Client mosq_sub1 received PUBLISH (d0, q0, r0, m0, 'pool/filter', ... (2 bytes))
on
Client mosq_sub1 received PUBLISH (d0, q0, r0, m0, 'pool/power', ... (2 bytes))
on
Client mosq_sub1 received PUBLISH (d0, q0, r0, m0, 'pool/heater', ... (2 bytes))
on
Client mosq_sub1 received PUBLISH (d0, q0, r0, m0, 'pool/power', ... (3 bytes))
off
Client mosq_sub1 received PUBLISH (d0, q0, r0, m0, 'pool/heater', ... (7 bytes))
standby
Client mosq_sub1 received PUBLISH (d0, q0, r0, m0, 'pool/bubble', ... (2 bytes))
on
Client mosq_sub1 received PUBLISH (d0, q0, r0, m0, 'pool/filter', ... (3 bytes))
off
Client mosq_sub1 received PUBLISH (d0, q0, r0, m0, 'pool/heater', ... (3 bytes))
off
Client mosq_sub1 received PUBLISH (d0, q0, r0, m0, 'pool/bubble', ... (3 bytes))
off
Client mosq_sub1 received PUBLISH (d0, q0, r0, m0, 'pool/filter', ... (2 bytes))
on
Client mosq_sub1 received PUBLISH (d0, q0, r0, m0, 'pool/heater', ... (7 bytes))
standby
Client mosq_sub1 received PUBLISH (d0, q0, r0, m0, 'wifi/state', ... (6 bytes))
online
Client mosq_sub1 received PUBLISH (d0, q0, r0, m0, 'pool/filter', ... (3 bytes))
off
Client mosq_sub1 received PUBLISH (d0, q0, r0, m0, 'pool/heater', ... (3 bytes))
off
Client mosq_sub1 received PUBLISH (d0, q0, r0, m0, 'pool/filter', ... (2 bytes))
on
Client mosq_sub1 received PUBLISH (d0, q0, r0, m0, 'pool/heater', ... (7 bytes))
standby
Client mosq_sub1 received PUBLISH (d0, q0, r0, m0, 'pool/filter', ... (3 bytes))
off
Client mosq_sub1 received PUBLISH (d0, q0, r0, m0, 'pool/heater', ... (3 bytes))
off
Client mosq_sub1 received PUBLISH (d0, q0, r0, m0, 'pool/filter', ... (2 bytes))
on
Client mosq_sub1 received PUBLISH (d0, q0, r0, m0, 'pool/heater', ... (7 bytes))
standby
Client mosq_sub1 received PUBLISH (d0, q0, r0, m0, 'pool/filter', ... (3 bytes))
off

This goes on and on and runs quite quickly and I believe there is a confusion of wires somewhere in my setup.

Of course, I might have some error in the electronics implementation as well. I tried to spot it, but this is quite hard, so I want to negate that there is confusion of the input wires as a first step.

I would be glad if somebody could post the colors !
Rhanks again for this fantastic project and the great documentation !

Happy Easter !

PS: As a newbie question: I see that I can enable debug messages via serial debug but I dont fully understand how this is meant. I guess that the esp has to be connected to a laptop then via USB (like during flashing). However, when connected to the pool at the same time, the 5V from the pool might confilct with the voltage from my laptop's USB port. Yes I know this is also 5V, but there might be small currents flowing from here to there nonetheless, no? Did you guys connect pool and laptop at the same time to the esp for debugging ? Seems way more comfortable for debugging than sending everything through mqtt, but I am worried to break my Laptop's usb port ... ?

stevengoossensB, 2025-04-22:
Had the same issue... Just found this back in the closed issues:

https://user-images.githubusercontent.com/69749534/121392224-7ce65000-c94f-11eb-8313-5aa678858860.png

CaptnRamius, 2025-04-25:
Thanks ! This looks exactly like what I was looking for !

CaptnRamius, 2025-04-26:
Hi again,
I have double-checked that all wires are connected as proposed. However, I still get "random" messages (reporting switching on and off for various states quickly back and forth). See the protocol above. It seems "in principle" something is sensed, but it is not interpreted in the right way, or not at the right speed.

I am using a D1 mini (AZ-delivery) at 160MHz.
I have no means to debug on the electrical signal level (like oscilloscope) besides measurung simple things like DC voltages, resistance, connectedness.
The next thing I could try is to enable debug messages, but - as stated in the previous post - I was hesitating to connect the D1 mini to the USB port of my computer while it is power through the pool at the same time. And I am not sure this would bring any useful information.
Anybody has a suggestion how to debug this ?
Thanks !

CaptnRamius, 2025-04-26:
Ok, I was searching again through the older closed issue and I found the recommendation to switch on SERIAL_DEBUG.
So I did that and received the following output, maybe somebody sees something ?
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

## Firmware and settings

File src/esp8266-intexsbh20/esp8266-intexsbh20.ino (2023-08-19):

/*
 * project:  Intex PureSpa WiFi Controller
 *
 * file:     esp8266-intexsbh20.ino
 *
 * encoding: UTF-8
 * created:  13th March 2021
 *
 * Copyright (C) 2021 Jens B.
 *
 *
 * Receive data handling of class PureSpaIO based on code from:
 *
 * DIYSCIP <https://github.com/yorffoeg/diyscip> (c) by Geoffroy HUBERT - yorffoeg@gmail.com
 *
 * DIYSCIP is licensed under a
 * Creative Commons Attribution-NonCommercial-ShareAlike 4.0 International License.
 *
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
 * SPDX-License-Identifier: CC-BY-NC-SA-4.0
 *
 */

/**
 * BUILD ENVIRONMENT:
 *
 * IDE: Arduino 1.8.19
 *
 * Libraries:
 *
 * - Arduino Core for ESP8266 3.1.2
 * - ArduinoJson 6.21.3
 * - PubSubClient (MQTT) 2.8
 *
 * Board: Wemos D1 mini (ESP8266)
 *
 * CPU:        160 MHz
 * Flash:      4M (FS: 1M, OTA: 1M)
 * Debug:      disabled
 * IwIP:       v2 lower memory
 * VTables:    IRAM
 * Exceptions: enabled
 *
 */

#include "common.h"
#include "ConfigurationFile.h"
#include "MQTTClient.h"
#include "MQTTPublisher.h"
#include "NTCThermometer.h"
#include "OTAUpdate.h"
#include "PureSpaIO.h"

#include <stdexcept>

ConfigurationFile config;
NTCThermometer thermometer;
OTAUpdate otaUpdate;
PureSpaIO pureSpaIO;

MQTTClient mqttClient;
MQTTPublisher mqttPublisher(mqttClient, pureSpaIO, thermometer);
String username;
String password;
String mqttPort;

unsigned long disconnectTime = 0;
LANG language = LANG::CODE;
bool initialized = false;


/**
 *  Arduino setup function
 */
void setup()
{
  Serial.begin(74880); // 74880 Baud is the default data rate of the ESP8266 bootloader

  // print versions
  Serial.printf_P(PSTR("%s MQTT WiFi Controller %s\n"), pureSpaIO.getModelName(), CONFIG::WIFI_VERSION);
  Serial.printf_P(PSTR("build with Arduino Core for ESP8266 %s\n"), ESP.getCoreVersion().c_str());
  Serial.printf_P(PSTR("based on Espressif NONOS SDK %s\n"), ESP.getSdkVersion());

  // try to load config file
  bool ready = false;
  if (config.load(CONFIG_TAG::FILENAME))
  {
    try
    {
      // init WiFi (station mode, DHCP, auto modem sleep after 10 s idle, auto wakeup every 100 ms * AP DTIM interval)
      WiFi.mode(WIFI_STA);
      WiFi.begin(config.get(CONFIG_TAG::WIFI_SSID), config.get(CONFIG_TAG::WIFI_PASSPHRASE));

      // init MQTT
      bool retainAll = config.exists(CONFIG_TAG::MQTT_RETAIN)? strcmp(config.get(CONFIG_TAG::MQTT_RETAIN), "no") != 0 : false;
      mqttPublisher.setRetainAll(retainAll);

      mqttClient.addMetadata(MQTT_TOPIC::MODEL, pureSpaIO.getModelName());
      mqttClient.addMetadata(MQTT_TOPIC::VERSION, CONFIG::WIFI_VERSION);

      mqttClient.addSubscriber(MQTT_TOPIC::CMD_BUBBLE, [](bool b) -> void { pureSpaIO.setBubbleOn(b); });
      mqttClient.addSubscriber(MQTT_TOPIC::CMD_FILTER, [](bool b) -> void { pureSpaIO.setFilterOn(b); });
      mqttClient.addSubscriber(MQTT_TOPIC::CMD_HEATER, [](bool b) -> void { pureSpaIO.setHeaterOn(b); });
      mqttClient.addSubscriber(MQTT_TOPIC::CMD_POWER,  [](bool b) -> void { pureSpaIO.setPowerOn(b); });
      mqttClient.addSubscriber(MQTT_TOPIC::CMD_WATER,  [](int i) -> void { pureSpaIO.setDesiredWaterTempCelsius(i); });
      if (pureSpaIO.getModel() == PureSpaIO::MODEL::SJBHS)
      {
        mqttClient.addSubscriber(MQTT_TOPIC::CMD_DISINFECTION, [](int i) -> void { pureSpaIO.setDisinfectionTime(i); });
        mqttClient.addSubscriber(MQTT_TOPIC::CMD_JET,          [](bool b) -> void { pureSpaIO.setJetOn(b); });
      }

      // enable OTA update if URL is defined in config
      if (config.exists(CONFIG_TAG::WIFI_OTA_URL))
      {
        mqttClient.addSubscriber(MQTT_TOPIC::CMD_OTA,  [](bool b) -> void { if (b) otaUpdate.start(config.get(CONFIG_TAG::WIFI_OTA_URL), mqttClient); });
      }

      // set language of error message if defined in config
      if (config.exists(CONFIG_TAG::MQTT_ERROR_LANG))
      {
        String lang = config.get(CONFIG_TAG::MQTT_ERROR_LANG);
        language = lang == "EN"? LANG::EN : (lang == "DE"? LANG::DE : LANG::CODE);
      }

      // init MQTT client
      if (config.exists(CONFIG_TAG::MQTT_USER))
      {
        username = config.get(CONFIG_TAG::MQTT_USER);
        password = config.get(CONFIG_TAG::MQTT_PASSWORD);
      }
      uint16 mqttPort;
      if (config.exists(CONFIG_TAG::MQTT_PORT))
      {
        mqttPort = atoi(config.get(CONFIG_TAG::MQTT_PORT));
      }
      else
      {
        mqttPort = 1883;
      }
      mqttClient.setup(config.get(CONFIG_TAG::MQTT_SERVER), mqttPort, username.c_str(), password.c_str(), pureSpaIO.getModelName(), MQTT_TOPIC::STATE, "offline");

      // init NTC thermometer
      thermometer.setup(22000, 3.33f, 320.f/100.f); // measured: 21990, 3.327f, 319.f/99.6f

      // enable hardware watchdog (8.3 s) by disabling software watchdog
      ESP.wdtDisable();

      ready = true;
    }
    catch (const std::runtime_error& re)
    {
      Serial.println(re.what());
    }
  }

  // stop CPU if init failed
  if (!ready)
  {
    ESP.deepSleep(ESP.deepSleepMax(), RF_DISABLED);
  }
}

/**
 * Arduino loop function
 */
void loop()
{
  // keep hardware watchdog alive
  ESP.wdtFeed();

  wl_status_t wifiStatus = WiFi.status(); //  WL_IDLE_STATUS 0, WL_NO_SSID_AVAIL 1, WL_SCAN_COMPLETED 2, WL_CONNECTED 3, WL_CONNECT_FAILED 4, WL_CONNECTION_LOST 5, WL_DISCONNECTED 6, WL_NO_SHIELD 255
  unsigned long now = millis();
  if (wifiStatus == WL_CONNECTED)
  {
    // WiFi is connected
    disconnectTime = 0;

    if (!initialized)
    {
      // publish client IP address
      mqttClient.addMetadata(MQTT_TOPIC::IP, WiFi.localIP().toString().c_str());

      // init whirlpool I/O after first WiFi connect
      pureSpaIO.setup(language);
      initialized = true;
    }
    else
    {
      // update MQTT
      mqttClient.loop();
      mqttPublisher.loop();

      // update pool
      pureSpaIO.loop();

      // force idle
      delay(100);
    }
  }
  else
  {
    // restart ESP8266 if WiFi connection cannot be established
    if (!disconnectTime)
    {
      // WiFi disconnected
      disconnectTime = now;
    }
    else if (timeDiff(now, disconnectTime) > CONFIG::WIFI_MAX_DISCONNECT_DURATION)
    {
      // WiFi disconnected too long, restart ESP
      DEBUG_MSG("restarting ... (no WiFi connection for several minutes)\n");
      ESP.restart();
    }
  }
}

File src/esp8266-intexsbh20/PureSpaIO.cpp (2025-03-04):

/*
 * project:  Intex PureSpa SB-H20 WiFi Controller
 *
 * file:     PureSpaIO.cpp
 *
 * encoding: UTF-8
 * created:  14th March 2021
 *
 * Copyright (C) 2021 Jens B.
 *
 *
 * Receive data handling based on code from:
 *
 * DIYSCIP <https://github.com/yorffoeg/diyscip> (c) by Geoffroy HUBERT - yorffoeg@gmail.com
 *
 * DIYSCIP is licensed under a
 * Creative Commons Attribution-NonCommercial-ShareAlike 4.0 International License.
 *
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
 * SPDX-License-Identifier: CC-BY-NC-SA-4.0
 *
 */

#include "PureSpaIO.h"

#include <ESP8266WiFi.h>


#if defined MODEL_SB_H20

#define DEFAULT_MODEL_NAME "Intex PureSpa SB-H20"

// bit mask for LEDs
namespace FRAME_LED
{
  const uint16 POWER          = 0x0001;
  const uint16 HEATER_ON      = 0x0080;  // max. 72 h, will start filter, will not stop filter
  const uint16 NO_BEEP        = 0x0100;
  const uint16 HEATER_STANDBY = 0x0200;
  const uint16 BUBBLE         = 0x0400;  // max. 30 min
  const uint16 FILTER         = 0x1000;  // max. 24 h
}

// bit mask of button
namespace FRAME_BUTTON
{
  const uint16 FILTER    = 0x0002;
  const uint16 BUBBLE    = 0x0008;
  const uint16 TEMP_DOWN = 0x0080;
  const uint16 POWER     = 0x0400;
  const uint16 TEMP_UP   = 0x1000;
  const uint16 TEMP_UNIT = 0x2000;
  const uint16 HEATER    = 0x8000;
}

#elif defined MODEL_SJB_HS

#define DEFAULT_MODEL_NAME "Intex PureSpa SJB-HS"

// bit mask for LEDs
namespace FRAME_LED
{
  const uint16 POWER          = 0x0001;
  const uint16 BUBBLE         = 0x0002;  // max. 30 min
  const uint16 HEATER_ON      = 0x0080;  // max. 72 h, will start filter, will not stop filter
  const uint16 NO_BEEP        = 0x0100;
  const uint16 HEATER_STANDBY = 0x0200;
  const uint16 JET            = 0x0400;
  const uint16 FILTER         = 0x1000;  // max. 24 h
  const uint16 DISINFECTION   = 0x2000;  // max. 8 h
}

// bit mask of button
namespace FRAME_BUTTON
{
  const uint16 DISINFECTION = 0x0001;
  const uint16 BUBBLE       = 0x0002;
  const uint16 JET          = 0x0008;
  const uint16 FILTER       = 0x0080;
  const uint16 TEMP_DOWN    = 0x0200;
  const uint16 POWER        = 0x0400;
  const uint16 TEMP_UP      = 0x1000;
  const uint16 TEMP_UNIT    = 0x2000;
  const uint16 HEATER       = 0x8000;
}

#endif

#ifdef CUSTOM_MODEL_NAME
const char MODEL_NAME[] = CUSTOM_MODEL_NAME;
#else
const char MODEL_NAME[] = DEFAULT_MODEL_NAME;
#endif  

namespace FRAME_DIGIT
{
  // bit mask of 7-segment display selector
  const uint16 POS_1 = 0x0040;
  const uint16 POS_2 = 0x0020;
  const uint16 POS_3 = 0x0800;
  const uint16 POS_4 = 0x0004;

  // bit mask of 7-segment display element
  const uint16 SEGMENT_A  = 0x2000;
  const uint16 SEGMENT_B  = 0x1000;
  const uint16 SEGMENT_C  = 0x0200;
  const uint16 SEGMENT_D  = 0x0400;
  const uint16 SEGMENT_E  = 0x0080;
  const uint16 SEGMENT_F  = 0x0008;
  const uint16 SEGMENT_G  = 0x0010;
  const uint16 SEGMENT_DP = 0x8000;
  const uint16 SEGMENTS   = SEGMENT_A | SEGMENT_B | SEGMENT_C | SEGMENT_D | SEGMENT_E | SEGMENT_F | SEGMENT_G;

  // bit mask of human readable value on 7-segment display
  const uint16 OFF   = 0x0000;
  const uint16 NUM_0 = SEGMENT_A | SEGMENT_B | SEGMENT_C | SEGMENT_D | SEGMENT_E | SEGMENT_F;
  const uint16 NUM_1 = SEGMENT_B | SEGMENT_C;
  const uint16 NUM_2 = SEGMENT_A | SEGMENT_B | SEGMENT_G | SEGMENT_E | SEGMENT_D;
  const uint16 NUM_3 = SEGMENT_A | SEGMENT_B | SEGMENT_C | SEGMENT_D | SEGMENT_G;
  const uint16 NUM_4 = SEGMENT_F | SEGMENT_G | SEGMENT_B | SEGMENT_C;
  const uint16 NUM_5 = SEGMENT_A | SEGMENT_F | SEGMENT_G | SEGMENT_C | SEGMENT_D;
  const uint16 NUM_6 = SEGMENT_A | SEGMENT_F | SEGMENT_E | SEGMENT_D | SEGMENT_C | SEGMENT_G;
  const uint16 NUM_7 = SEGMENT_A | SEGMENT_B | SEGMENT_C;
  const uint16 NUM_8 = SEGMENT_A | SEGMENT_B | SEGMENT_C | SEGMENT_D | SEGMENT_E | SEGMENT_F | SEGMENT_G;
  const uint16 NUM_9 = SEGMENT_A | SEGMENT_B | SEGMENT_C | SEGMENT_D | SEGMENT_F | SEGMENT_G;
  const uint16 LET_A = SEGMENT_E | SEGMENT_F | SEGMENT_A | SEGMENT_B | SEGMENT_C | SEGMENT_G;
  const uint16 LET_C = SEGMENT_A | SEGMENT_F | SEGMENT_E | SEGMENT_D;
  const uint16 LET_D = SEGMENT_B | SEGMENT_C | SEGMENT_D | SEGMENT_E | SEGMENT_G;
  const uint16 LET_E = SEGMENT_A | SEGMENT_F | SEGMENT_E | SEGMENT_D | SEGMENT_G;
  const uint16 LET_F = SEGMENT_E | SEGMENT_F | SEGMENT_A | SEGMENT_G;
  const uint16 LET_H = SEGMENT_B | SEGMENT_C | SEGMENT_E | SEGMENT_F | SEGMENT_G;
  const uint16 LET_N = SEGMENT_A | SEGMENT_B | SEGMENT_C | SEGMENT_E | SEGMENT_F;
}

// frame type markers
namespace FRAME_TYPE
{
  const uint16 CUE    = 0x0100;
  const uint16 LED    = 0x4000;
  const uint16 DIGIT  = FRAME_DIGIT::POS_1 | FRAME_DIGIT::POS_2 | FRAME_DIGIT::POS_3 | FRAME_DIGIT::POS_4;

#if defined MODEL_SB_H20
  const uint16 BUTTON = CUE | FRAME_BUTTON::POWER | FRAME_BUTTON::FILTER | FRAME_BUTTON::HEATER | FRAME_BUTTON::BUBBLE | FRAME_BUTTON::TEMP_UP | FRAME_BUTTON::TEMP_DOWN | FRAME_BUTTON::TEMP_UNIT;
#elif defined MODEL_SJB_HS
  const uint16 BUTTON = CUE | FRAME_BUTTON::POWER | FRAME_BUTTON::FILTER | FRAME_BUTTON::HEATER | FRAME_BUTTON::BUBBLE | FRAME_BUTTON::TEMP_UP | FRAME_BUTTON::TEMP_DOWN | FRAME_BUTTON::TEMP_UNIT | FRAME_BUTTON::DISINFECTION | FRAME_BUTTON::JET;
#endif
}

namespace DIGIT
{
  // 7-segment display update control
  const uint8 POS_1     = 0x8;
  const uint8 POS_2     = 0x4;
  const uint8 POS_3     = 0x2;
  const uint8 POS_4     = 0x1;
  const uint8 POS_1_2   = POS_1 | POS_2;
  const uint8 POS_1_2_3 = POS_1 | POS_2 | POS_3;
  const uint8 POS_ALL   = POS_1 | POS_2 | POS_3 | POS_4;

  // ASCII values used to map non-numeric states of the 7-segment display
  const char OFF = ' ';
};
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

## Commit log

2021-04-03 initial checkin
    [ConfigurationFile.h]
2021-04-04 added photos of cable tree and perfboard to README
2022-05-22 added photos of perfboard bottom and open case
2022-05-22 PCB added
    - added PCB subdirectory with Gerber files, Fritzing files and photos
    - README updated
    [Pool SB-H20 WiFi MQTT.fzz]
2022-07-10 config file read buffer size increased
    adding MQTT authentication has increased the typical size of the config file
    [ConfigurationFile.h]
2023-05-04 added missing return statements
    ConfigurationFile.cpp, MQTTClient.cpp, SBH20IO.cpp
    [SBH20IO.cpp]
2023-05-30 PureSpaIO getModelName(): fix non-const return value, init model in header file
    [PureSpaIO.cpp, PureSpaIO.h]
2023-05-31 PureSpaIO::setJetOn(): fix checking jet status
    [PureSpaIO.cpp, common.h]
2023-06-21 added link for 3D model of a case incl. attachment
2023-08-04 convert 7 segement symbols to ASCII (instead of nibbles) to resolve limitation to 16 symbols
    [PureSpaIO.cpp, PureSpaIO.h]
2023-08-04 provide error code instead of error value, added disinfection time for model SJB-HS - modified decodeDisplay(): inverted byte order of display value (e.g. to make error code readable as string) - mod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
    [PureSpaIO.cpp, PureSpaIO.h, common.h]
2023-08-04 added build option FORCE_WIFI_SLEEP to test alternatives for setting the water temperature without interrupting MQTT connection
2023-08-04 added GitHub Action to test build Arduino sketch
2023-08-04 set desired water temperature without interrupting MQTT connection - PureSpaIO::setDesiredWaterTempCelsius: read back actual setpoint - PureSpaIO::decodeButton: cancel temp up/down if buzzer is on - 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
    [PureSpaIO.cpp, PureSpaIO.h, common.h]
2023-08-04 improved reliablity of setting desired water temperatur - PureSpaIO::setDesiredWaterTempCelsius: repeat intial change on failure (more robust) - PureSpaIO::setDesiredWaterTempCelsius: skip getting ac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
    [PureSpaIO.cpp, PureSpaIO.h, common.h]
2023-08-04 improve reliablity of setting desired water temperatur - introduce constant PureSpaIO::BUTTON_FRAMES to make PureSpaIO::TOTAL_FRAMES depended on pool model - introduce constant PureSpaIO::BUTTON::PRE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
    [PureSpaIO.cpp, PureSpaIO.h, common.h]
2023-08-12 moved firmware code into src folder
    [ConfigurationFile.h]
2023-08-12 fixed compiler warnings (ICACHE_RAM_ATTR deprecated, catch polymorphic type by value)
    [PureSpaIO.cpp, PureSpaIO.h, common.h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]
2023-08-12 moved config data into src folder (required by Arduino ESP8266 LittleFS Filesystem Uploader)
2023-08-19 updated dependencies (Arduino Core for ESP8266 3.1.2, ArduinoJson 6.21.3)
2023-08-22 fixed compiler warnings (comparison of constant is always true, catching polymorphic type by value)
    [common.h]

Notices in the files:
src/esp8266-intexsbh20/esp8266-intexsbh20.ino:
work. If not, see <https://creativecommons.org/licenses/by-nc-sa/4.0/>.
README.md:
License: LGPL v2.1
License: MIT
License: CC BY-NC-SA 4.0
